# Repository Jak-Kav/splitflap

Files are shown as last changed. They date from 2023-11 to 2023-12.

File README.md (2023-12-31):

# DIY Split-Flap Display<br />(Modified by James Kavanagh (jk620))

This project is taken from `scottbez1/splitflap` and has been modofied to suit my needs.    
This is a 6 module display, with lasercut mechanical parts and base.    
I am using the chainlink system (v1.1) and the chainlink buddy (PCB version) with a lilygo T-Display.    
The system will connect to WiFi, and then NTP. It will display the time as a 24 hour clock. It will automatically adjust for daylight savings time in the UK.     
It will automaitically display 'LUNCH'  between 11:59 and 12:01 every day.     
It will automatically display 'HOME' between 16:59 and 17:01 every day.    
It will automatically display 'TINKER' between 18:00 and 18:10 on Wednesday only.    

The device will also start a bluetooth characteristic and broadcast it's current IP address. That way, you can connect to the device via bluetooth to discover it's IP address, and then connect to the webserver on the device. Oonce connected to the webserver, you are greeted with a simple HTML page where you can input a message (upto 6 characters long), and as long as it has been more than 10 minuets since the last custom message was displayed via the webserver, then your message will be displayed.    
There is also the option to manually force reset/recalibrate the device via the webserver, but you will need the password to do this (prevent spamming), and the password is in the code.

The entry point to the code is:    
`arduino/splitflap/esp32/splitflap/main.cpp`    
When editing the project, make sure you are using PlatformIO, and make sure the enviornment is set to `chainlink`. This is the only one that will work with the hardware and mechanical options implemented.

### BUILD & RELEASE
You can push commit to this repo as normal. The GitHub Actions will always bulid the firmware and confirm that it compiles and builds ok.    
If the commit is ready for a build and _RELEASE_, then simply add `*RELEASE*` to the commit message followed by `*V*` and a version number.    
I.e., `Feature X Added - *RELEASE* *V* 1.1.0` and this will build the firmware and automatically create a GitHub Release with that version number. 

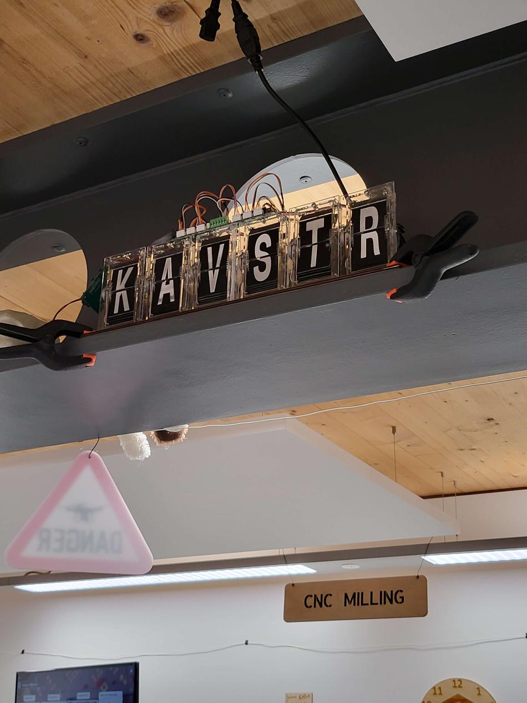
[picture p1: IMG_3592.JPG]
My Finished Display


Below is the original README:    
- - - - - -
This is a DIY [split-flap display](https://en.wikipedia.org/wiki/Split-flap_display).
Prototype four-character display: [video](https://www.youtube.com/watch?v=vq4o_88kN8g).

animated rendering
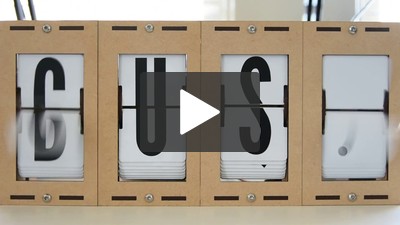
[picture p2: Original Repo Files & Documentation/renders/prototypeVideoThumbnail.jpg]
prototype video (https://www.youtube.com/watch?v=vq4o_88kN8g)






The goal is to make a low-cost display that's easy to fabricate at home in small/single quantities (e.g. custom materials can be ordered from Ponoko or similar, and other hardware is generally available).

You can view an interactive 3d model of the design on the [project website](https://scottbez1.github.io/splitflap/).

The [splitflap community Discord server](https://discord.com/invite/wgehm3PcrC) is the best place to keep up with the latest changes or ask questions about the project!

Want to help support development or just say "thanks"? Consider a one-time or monthly sponsorship:

| [:heart: Sponsor scottbez1 on GitHub](https://github.com/sponsors/scottbez1) |
|---|

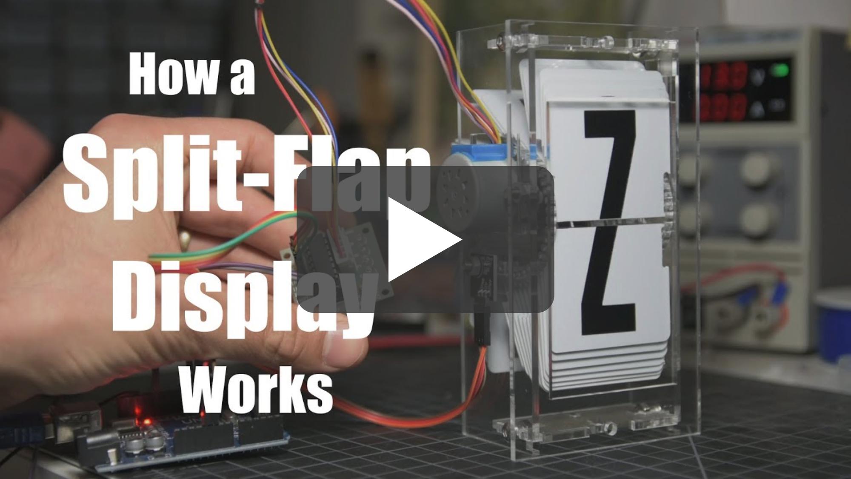
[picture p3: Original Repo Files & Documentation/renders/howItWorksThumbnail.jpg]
Video: how a split-flap display works (https://www.youtube.com/watch?v=UAQJJAQSg_g)


**Using this project in a commercial setting or for paid client work?** Go right ahead - it's open source (just make sure to follow the terms of the Apache License)! I would, however, ask that you consider [sponsoring the project](https://github.com/sponsors/scottbez1). I've been developing and maintaining this project in my free time for over 6 years, and I'd love to continue working on it. Sponsorships allow me to pay for prototypes and development tools that make this project possible. Unlike pure software projects, every iteration has real hardware costs; sponsorships allow me to keep iterating and improving the project faster. Thank you!

# Current Status
[You can download the **latest stable release** from the official 'releases' page.](https://github.com/scottbez1/splitflap/releases)

Releases have been tested and used to produce working units, but as this is a continuously evolving open-source project, there may always be minor issues and/or incomplete documentation from time to time.

| Component | Status | Notes |
| --- | --- | --- |
| Enclosure/Mechanics | *Stable* | |
| Classic Controller Electronics | *Stable* | |
| Firmware | *Stable* | |
| Control Software Example | *Stable* | Example python code for driving the display is in the [software](software) directory|

:bulb: There's a new electronics system, called the *Chainlink* system (more on this [below](#chainlink-electronics)), which makes assembly easier and supports larger displays (100+ modules), using an ESP32 for the controller. It's stable and recommended over the older "Classic" controller for new builds.

Here's a video of a large 108-module display powered by 18 Chainlink Driver boards and a Chainlink Base:

Video: animations on 108-module display (https://youtu.be/g9EPabcxBsM)

I'd love to hear your thoughts and questions about this project, and happy to incorporate any feedback you might have into these designs! Please feel free (and encouraged) to [open GitHub issues](https://github.com/scottbez1/splitflap/issues/new), email me directly, reach out [on Twitter](https://twitter.com/scottbez1), and [get involved](https://github.com/scottbez1/splitflap/pulls) in the open source development and let's keep chatting and building together!

# Build Your Own
Please note, updated documentation for the Chainlink system is still in progress; you may see outdated references to the "Classic" electronics in some documentation in the meantime. If you have any questions, please don't hesitate to ask in the [community Discord server](https://discord.gg/Hxnftc8PyW)!

* [**Ordering guide (the "easy" route) - updated for Chainlink**](https://paper.dropbox.com/doc/Splitflap-Ordering-the-easy-route--BsXzf8VyILR3nl1vUpOi28TWAg-0i6r3aqw6kZVXQOP2MyNr)
* [**Chainlink Driver Electronics User Guide**](https://paper.dropbox.com/doc/Chainlink-Driver-v1.1-Electronics-User-Guide--BsVuP9OHVo952_ZdJDBomCCzAg-U0DAXrSxEoOhgSoRU39hq)
* [**Latest stable release**](https://github.com/scottbez1/splitflap/releases)
* [**Assembly instructions (v0.5/0.6/0.7)**](https://paper.dropbox.com/doc/Splitflap-Kit-v0.5v1.0-Instructions--ASQDu1uoa6n4_t1pva1bM1MgAg-bxXJlke5ROmamcx4OH44r)

# Table of Contents
- [DIY Split-Flap Display(Modified by James Kavanagh (jk620))](#diy-split-flap-displaymodified-by-james-kavanagh-jk620)
- [Current Status](#current-status)
- [Build Your Own](#build-your-own)
- [Table of Contents](#table-of-contents)
- [Design Overview](#design-overview)
  - [Mechanical](#mechanical)
  - [Electronics](#electronics)
    - [Module Electronics](#module-electronics)
    - [Chainlink Electronics](#chainlink-electronics)
      - [Chainlink Driver](#chainlink-driver)
      - [Chainlink Buddy \[T-Display\]](#chainlink-buddy-t-display)
      - [Chainlink Buddy \[Breadboard\]](#chainlink-buddy-breadboard)
      - [Chainlink Base](#chainlink-base)
    - [Classic Controller Electronics (deprecated)](#classic-controller-electronics-deprecated)
    - [Miscellaneous Tools](#miscellaneous-tools)
      - [Flaps and Fonts](#flaps-and-fonts)
      - [3D Printed Tools](#3d-printed-tools)
      - [Chainlink Driver Tester](#chainlink-driver-tester)
  - [Code](#code)
    - [Firmware](#firmware)
    - [Computer Control Software](#computer-control-software)
- [Contributing/Modifying](#contributingmodifying)
  - [3D Design](#3d-design)
    - [Rendering](#rendering)
      - [Laser-cut vector files](#laser-cut-vector-files)
      - [Animated gif](#animated-gif)
      - [STL models/web viewer](#stl-modelsweb-viewer)
  - [Electronics Design](#electronics-design)
    - [Rendering](#rendering-1)
- [License](#license)

# Design Overview

## Mechanical
The mechanical/structural components are made from laser-cut 3mm MDF or acrylic, and held together with M4 bolts and nuts. The design is parametric and built using OpenSCAD. See below for more info on rendering/modifying the design.

2d laser cut rendering

Latest auto-generated (untested!) artifacts<sup>:warning:</sup>:
* For Ponoko 3mm MDF ([1x svg](https://s3.amazonaws.com/splitflap-artifacts/master/3d/3d_laser_vector-ponoko-3mm-mdf_1x.svg), [4x svg](https://s3.amazonaws.com/splitflap-artifacts/master/3d/3d_laser_vector-ponoko-3mm-mdf_4x.svg))
* For Ponoko 3mm acrylic ([1x svg](https://s3.amazonaws.com/splitflap-artifacts/master/3d/3d_laser_vector-ponoko-3mm-acrylic_1x.svg), [4x svg](https://s3.amazonaws.com/splitflap-artifacts/master/3d/3d_laser_vector-ponoko-3mm-acrylic_4x.svg),)
* For generic material (0.18mm kerf correction) ([1x svg](https://s3.amazonaws.com/splitflap-artifacts/master/3d/3d_laser_vector.svg))
* For Elecrow 3mm Wood ([1x zipped pdf](https://s3.amazonaws.com/splitflap-artifacts/master/3d/3d_laser_vector-elecrow-3mm-wood_1x.zip), note that Elecrow orders are automatically 5x)
* For Elecrow 3mm Acrylic ([1x zipped pdf](https://s3.amazonaws.com/splitflap-artifacts/master/3d/3d_laser_vector-elecrow-3mm-acrylic_1x.zip), note that Elecrow orders are automatically 5x)

<sup>:warning:</sup>For tested/stable/recommended artifacts, use the [latest release](https://github.com/scottbez1/splitflap/releases) instead

## Electronics
For small displays (up to 3 modules), you can skip the custom controller boards and use off-the-shelf ULN2003A driver
modules plugged into an Arduino Uno. This is [partially documented in the wiki](https://github.com/scottbez1/splitflap/wiki/Electronics#basic-prototyping-alternative-electronics-approach)
but may require some additional tinkering to get it to work. _Help wanted: if you'd like to help improve these instructions,
please reach out in the Discord server, thanks!_

The Chainlink electronics system is the current recommended design, which allows for larger-scale displays by chaining more
modules together and uses a more powerful microcontroller (ESP32) compared to the older "Classic" controller. It also adds 
the possibility of wifi and BLE control, though firmware support for this is very limited for now.

The older design ("Classic" controller board), which plugs into an Arduino Uno as a shield and can control up to 4 modules is
no longer recommended and will not receive firmware updates going forward. New builds are recommended to use the Chainlink
ESP32-based system instead.

### Module Electronics
Each module needs a hall-effect sensor for start-up calibration and fault monitoring. This can be mounted in
[different ways](https://github.com/scottbez1/splitflap/wiki/Electronics#sensor-board-alternative) but the recommended
approach is to use a small PCB, with an AH3391Q (or similar) sensor and connector, which mounts to the side of the
module with a single screw and can easily be adjusted for precise calibration.

These boards are small (about 16mm x 16 mm) and the designs are available as a panelized PCB, which can be snapped
apart. The panelization is configurable and is optimized for production at low-cost PCB fabricators like SeeedStudio, JLCPCB, or PCBWay.

<a href="https://s3.amazonaws.com/splitflap-artifacts/master/electronics/sensor-panelized-pcb-raster.png">

</a>

Latest auto-generated (untested!) artifacts<sup>:warning:</sup>:

* Sensor PCB, single ([gerbers](https://s3.amazonaws.com/splitflap-artifacts/master/electronics/sensor-jlc/gerbers.zip) / [pdf](https://s3.amazonaws.com/splitflap-artifacts/master/electronics/sensor-pcb-packet.pdf))
* Sensor PCB, panelized ([gerbers](https://s3.amazonaws.com/splitflap-artifacts/master/electronics/sensor-panelized-jlc/gerbers.zip) / [pdf](https://s3.amazonaws.com/splitflap-artifacts/master/electronics/sensor-panelized-pcb-packet.pdf))

<sup>:warning:</sup>For tested/stable/recommended artifacts, use the [latest release](https://github.com/scottbez1/splitflap/releases) instead

### Chainlink Electronics
The Chainlink system replaces the older "Classic" controller electronics and is designed to support long chains of driver boards
to control large displays (think 100+ split-flap modules). It's also designed to be easy and cheap to build, especially in higher
quantities, due to its simple BOM and surface-mount components.

The Chainlink system requires 2 core elements:
* One or more **Chainlink Driver** board. This is what interfaces with the motors and sensors of each module. Each Driver board
supports up to **6** individual split-flap modules. Chainlink Driver boards can be chained together to construct a large display.
* Some kind of ESP32 microcontroller board. There are a few options:
    * For small/medium displays, one of the **Chainlink Buddy** boards are recommended
        * **Chainlink Buddy [T-Display]**  holds a Lilygo T-Display ESP32 module which includes a built-in LCD and 2 buttons
        * **Chainlink Buddy [Breadboard]** makes it easy to connect a Chainlink Driver to a breadboard for prototyping, though you can also easily connect a Chainlink Driver to a breadboard with a few dupont wires.
    * For large displays, the **Chainlink Base** provides a number of advanced features: central
power management/distribution and fault monitoring, UART and RS-485 connections, configuration switches, and status LEDs.

#### Chainlink Driver
<a href="https://s3.amazonaws.com/splitflap-artifacts/master/electronics-chainlink/chainlinkDriver-3d.png">

</a>

Key features (compared to the older "Classic" Controller):
* Controls 6 split-flap modules per board instead of just 4 - fewer PCBs means lower cost and less wiring
* Longer PCB (200mm) gets connectors closer to each module so wires have more slack
* Primarily SMD and all components (except the pin headers and motor connectors) are available in JLCPCB's parts library
for easy SMD/THT assembly
* Clock and latch lines are buffered on each board with a 74HC125 to support longer chains
* Neopixels replaced by shift-register-driven single-color LED per module (one fewer data line needed in the chain, lower current draw, and 3.3v IO friendly)
* 2 bits of loopback (connecting 2 spare output bits on output shift registers to 2 spare inputs) allows the controller
to validate data integrity up and down the whole chain
* ~~TPL7407L mosfet low-side drivers instead of ULN2003A/MIC5842 (lower on-resistance means less voltage drop in the driver = more torque, less waste heat, and less total current consumption)~~
Due to the chip shortage, TPL7407L ICs are not currently available and will likely not be available again until mid-2022, so the auto-generated
JLC component/bom files below currently use ULN2003A darlington drivers as a suitable drop-in replacement.
* Module order goes from right-to-left since this is intended to be installed and accessed from *behind* the modules

Chainlink Driver boards are [available mostly-assembled in the Bezek Labs store](https://www.etsy.com/listing/1123280069/splitflap-chainlink-driver-v11),
and come with the additional connectors and ribbon cables you'll need. Purchases support continued development of this project.

More information on building and using Chainlink Drivers is available in the [Chainlink Driver User Guide](https://paper.dropbox.com/doc/Chainlink-Driver-v1.1-Electronics-User-Guide--BW2lxdjVkAxva68kYw2doWQEAg-U0DAXrSxEoOhgSoRU39hq).

Or if you'd like to order these directly from a fab, this design is optimized for assembly at JLCPCB, and files are automatically generated
for ordering *assembled* PCBs there. Or if you wish to assemble this board yourself instead of paying for assembly, 
you can view the [interactive BOM/placement tool](https://s3.amazonaws.com/splitflap-artifacts/master/electronics-chainlink/bom/chainlinkDriver-ibom.html)

Depending on available stock at JLCPCB, you may need to manually modify the BOM file to use alternative components, or regenerate the files
yourself using `export_jlcpcb.py` and specifying one or more `LCSC_ALT_*` field names to use a pre-selected alternative part number. See
the schematic for available pre-selected alternatives (check the symbol's properties/fields).

<a href="https://s3.amazonaws.com/splitflap-artifacts/master/electronics-chainlink/chainlinkDriver-schematic.pdf">

</a>

<a href="https://s3.amazonaws.com/splitflap-artifacts/master/electronics-chainlink/chainlinkDriver-pcb-raster.png">

</a>

Latest auto-generated (untested!) artifacts<sup>:warning:</sup>:

* Schematic [pdf](https://s3.amazonaws.com/splitflap-artifacts/master/electronics-chainlink/chainlinkDriver-schematic.pdf)
* PCB overview [pdf](https://s3.amazonaws.com/splitflap-artifacts/master/electronics-chainlink/chainlinkDriver-pcb-packet.pdf)
* PCB gerbers [zip](https://s3.amazonaws.com/splitflap-artifacts/master/electronics-chainlink/chainlinkDriver-jlc/gerbers.zip)
* PCB bom (for JLCPCB assembly) [csv](https://s3.amazonaws.com/splitflap-artifacts/master/electronics-chainlink/chainlinkDriver-jlc/bom.csv)
* PCB CPL (for JLCPCB assembly) [csv](https://s3.amazonaws.com/splitflap-artifacts/master/electronics-chainlink/chainlinkDriver-jlc/pos.csv)
* PCB bom (for manual assembly) [interactive](https://s3.amazonaws.com/splitflap-artifacts/master/electronics-chainlink/bom/chainlinkDriver-ibom.html)

<sup>:warning:</sup>For tested/stable/recommended artifacts, use the [latest release](https://github.com/scottbez1/splitflap/releases) instead

#### Chainlink Buddy \[T-Display\]
<a href="https://s3.amazonaws.com/splitflap-artifacts/master/electronics-chainlink-buddy-t-display/chainlinkBuddyTDisplay-3d.png">

</a>

The Chainlink Buddy \[T-Display\] is a convenient way to connect a T-Display ESP32 board (recommended microcontroller) to a chain
of Chainlink Drivers.

Key features:
* TTGO T-Display ESP32 module as the controller, which includes USB-C, color IPS LCD display and buttons
* Extra terminals for every pin of the T-Display allow you to connect any other peripherals to the ESP32 (the connection to the Chainlink Driver requires _only 4_ of the GPIOs)
* Optional barrel jack makes it easy to use a "wall wart" AC adapter/power-supply (since the Chainlink Driver only has screw terminals for power) -- plug in a 12V supply
and then run a wire from the onboard screw terminals to the Chainlink Driver's motor power screw terminals.
* Optional 5V regulator allows for powering the ESP32 without a USB connection, using the 12V motor power supply

Chainlink Buddy \[T-Display\] boards are [available in the Bezek Labs store](https://www.etsy.com/listing/1109357786/splitflap-chainlink-buddy-t-display),
and come with the additional connectors you'll need. Purchases support continued development of this project. 

<a href="https://s3.amazonaws.com/splitflap-artifacts/master/electronics-chainlink-buddy-t-display/chainlinkBuddyTDisplay-schematic.pdf">

</a>

<a href="https://s3.amazonaws.com/splitflap-artifacts/master/electronics-chainlink-buddy-t-display/chainlinkBuddyTDisplay-pcb-raster.png">

</a>

Latest auto-generated (untested!) artifacts<sup>:warning:</sup>:

* Schematic [pdf](https://s3.amazonaws.com/splitflap-artifacts/master/electronics-chainlink-buddy-t-display/chainlinkBuddyTDisplay-schematic.pdf)
* PCB ([gerbers](https://s3.amazonaws.com/splitflap-artifacts/master/electronics-chainlink-buddy-t-display/chainlinkBuddyTDisplay-jlc/gerbers.zip) / [pdf](https://s3.amazonaws.com/splitflap-artifacts/master/electronics-chainlink-buddy-t-display/chainlinkBuddyTDisplay-pcb-packet.pdf))
* Panelized PCB ([gerbers](https://s3.amazonaws.com/splitflap-artifacts/master/electronics-chainlink-buddy-t-display/chainlinkBuddyTDisplay-panelized-jlc/gerbers.zip) / [pdf](https://s3.amazonaws.com/splitflap-artifacts/master/electronics-chainlink-buddy-t-display/chainlinkBuddyTDisplay-panelized-pcb-packet.pdf))
* PCB bom (for manual assembly) [interactive](https://s3.amazonaws.com/splitflap-artifacts/master/electronics-chainlink-buddy-t-display/bom/chainlinkBuddyTDisplay-ibom.html)

<sup>:warning:</sup>For tested/stable/recommended artifacts, use the [latest release](https://github.com/scottbez1/splitflap/releases) instead

#### Chainlink Buddy \[Breadboard\]
<a href="https://s3.amazonaws.com/splitflap-artifacts/master/electronics-chainlink-buddy-breadboard/chainlinkBuddyBreadboard-3d.png">

</a>

The Chainlink Buddy \[Breadboard\] makes it easy to connect a Chainlink Driver to a breadboard for prototyping. You could use 5 dupont wires and have a
messy rats nest, or you could use a single ribbon cable and this slick breakout board.

Chainlink Buddy \[Breadboard\] boards are [available in the Bezek Labs store](https://www.etsy.com/listing/1123863267/splitflap-chainlink-buddy-breadboard),
and come with the additional connectors you'll need. Purchases support continued development of this project. 

<a href="https://s3.amazonaws.com/splitflap-artifacts/master/electronics-chainlink-buddy-breadboard/chainlinkBuddyBreadboard-schematic.pdf">

</a>

<a href="https://s3.amazonaws.com/splitflap-artifacts/master/electronics-chainlink-buddy-breadboard/chainlinkBuddyBreadboard-pcb-raster.png">

</a>

Latest auto-generated (untested!) artifacts<sup>:warning:</sup>:

* Schematic [pdf](https://s3.amazonaws.com/splitflap-artifacts/master/electronics-chainlink-buddy-breadboard/chainlinkBuddyBreadboard-schematic.pdf)
* PCB ([gerbers](https://s3.amazonaws.com/splitflap-artifacts/master/electronics-chainlink-buddy-breadboard/chainlinkBuddyBreadboard-jlc/gerbers.zip) / [pdf](https://s3.amazonaws.com/splitflap-artifacts/master/electronics-chainlink-buddy-breadboard/chainlinkBuddyBreadboard-pcb-packet.pdf))
* Panelized PCB ([gerbers](https://s3.amazonaws.com/splitflap-artifacts/master/electronics-chainlink-buddy-breadboard/chainlinkBuddyBreadboard-panelized-jlc/gerbers.zip) / [pdf](https://s3.amazonaws.com/splitflap-artifacts/master/electronics-chainlink-buddy-breadboard/chainlinkBuddyBreadboard-panelized-pcb-packet.pdf))
* PCB bom (for manual assembly) [interactive](https://s3.amazonaws.com/splitflap-artifacts/master/electronics-chainlink-buddy-breadboard/bom/chainlinkBuddyBreadboard-ibom.html)

<sup>:warning:</sup>For tested/stable/recommended artifacts, use the [latest release](https://github.com/scottbez1/splitflap/releases) instead

#### Chainlink Base
<a href="https://s3.amazonaws.com/splitflap-artifacts/master/electronics-chainlink-base/chainlinkBase-3d.png">

</a>

This has been tested and appears to work, but is not yet recommended for general use. Firmware support is in progress.

The Chainlink Base PCB is an optional alternative to a Chainink Buddym, designed for particularly large displays.
It hosts the ESP32 and adds additional connectivity options (terminals for UART and RS485 serial) and
power distribution (independently-monitored power channels for multiple "zones" of Driver boards).

Key features:
* TTGO T-Display ESP32 module as the controller, which includes USB-C, color IPS LCD display and buttons
* Optional master relay output for 12V PSU control (5V relay, up to ~500mA coil current)
  * Future firmware will power on the 12V PSU after a startup self-test, and power off PSU in case of any faults
* 5 channels of independently monitored 12V switches for powering groups of Chainlink Driver boards (6-10A max per channel)
  * Depending on the motors you use, each channel may be able to power about 6 Chainlink Driver boards which is 36 splitflap modules
  * Each channel includes an automotive fuse holder for additional over-current protection
  * INA219 and shunt resistor provide high fidelity voltage and current monitoring 
  * Firmware will power on each channel after a startup self-test, and power off the channel in case of any faults
  * 3.3V output for powering many Chainlink Driver boards
* Flexible controller input power
  * USB power from the T-Display works by default, though external power is recommended for larger displays
  * Regulated 5V can be connected directly to the screw terminals, or
  * if you are using an always-on 12V PSU without a master relay, you can install a buck module and power the board from 12V using the 7-28V screw terminals

<a href="https://s3.amazonaws.com/splitflap-artifacts/master/electronics-chainlink-base/chainlinkBase-schematic.pdf">

</a>

<a href="https://s3.amazonaws.com/splitflap-artifacts/master/electronics-chainlink-base/chainlinkBase-pcb-raster.png">

</a>

Latest auto-generated (untested!) artifacts<sup>:warning:</sup>:

* Schematic [pdf](https://s3.amazonaws.com/splitflap-artifacts/master/electronics-chainlink-base/chainlinkBase-schematic.pdf)
* PCB overview [pdf](https://s3.amazonaws.com/splitflap-artifacts/master/electronics-chainlink-base/chainlinkBase-pcb-packet.pdf)
* PCB gerbers [zip](https://s3.amazonaws.com/splitflap-artifacts/master/electronics-chainlink-base/chainlinkBase-jlc/gerbers.zip)
* PCB bom (for manual assembly) [interactive](https://s3.amazonaws.com/splitflap-artifacts/master/electronics-chainlink-base/bom/chainlinkBase-ibom.html)

<sup>:warning:</sup>There are currently no stable releases of this board. Once the board design is tested and recommended, a stable release will be created on the [Releases dashboard](https://github.com/scottbez1/splitflap/releases)

### Classic Controller Electronics (deprecated)
The Classic driver board is not recommended for new designs.

The Classic controller board is designed to plug into an Arduino like a shield, and can control 4 stepper motors.
Up to 3 driver boards can be chained together, for up to 12 modules controlled by a single Arduino.
The designs for the controller can be found under [`electronics/splitflap.pro`](electronics/splitflap.pro) (KiCad 5 project).
Nearly everything is a through-hole component rather than SMD, so it's very easy to hand-solder.

The driver uses 2 MIC5842 low-side shift-register drivers, with built-in transient-suppression diodes, to control the motors, and a 74HC165 shift register to read from 4 hall-effect magnetic home position sensors.
There are optional WS2812B RGB LEDs which can be used to indicate the status of each of the 4 channels.

<a href="https://s3.amazonaws.com/splitflap-artifacts/master/electronics-classic/classic-schematic.pdf">

</a>

The PCB layout is 10cm x 5cm which makes it fairly cheap to produce using a low-cost PCB manufacturer (e.g. Seeed Studio).

<a href="https://s3.amazonaws.com/splitflap-artifacts/master/electronics-classic/classic-pcb-raster.png">

</a>

Latest auto-generated (untested!) artifacts<sup>:warning:</sup>:

* Bill of Materials ([csv](https://s3.amazonaws.com/splitflap-artifacts/master/electronics-classic/bom/splitflap-bom.csv), [interactive](https://s3.amazonaws.com/splitflap-artifacts/master/electronics-classic/bom/splitflap-ibom.html))
* PCB ([gerbers](https://s3.amazonaws.com/splitflap-artifacts/master/electronics-classic/classic-jlc/gerbers.zip) / [pdf](https://s3.amazonaws.com/splitflap-artifacts/master/electronics-classic/classic-pcb-packet.pdf))
* Panelized PCB ([gerbers](https://s3.amazonaws.com/splitflap-artifacts/master/electronics-classic/classic-panelized-jlc/gerbers.zip) / [pdf](https://s3.amazonaws.com/splitflap-artifacts/master/electronics-classic/classic-panelized-pcb-packet.pdf))

<sup>:warning:</sup>For tested/stable/recommended artifacts, use the [latest release](https://github.com/scottbez1/splitflap/releases) instead

### Miscellaneous Tools

#### Flaps and Fonts
If you'd like to print your own flaps, or cut custom vinyl letter stickers, the project includes a script to generate vector design files
that is extremely configurable:

* Font for text (this is further customizable in OpenSCAD)
* Character-set - which letters/numbers/symbols/colors are included and in what order
* Bleed - extends rendering past the borders of the flaps to compensate for slight misalignment of printing and cutting operations
* Keepout areas - option to highlight keepout violations for manual review, automatically clip them, or ignore them
* Rendering options:
    * Single-sided - useful for previewing how all letters will look on flaps
    * Front/back - for batch duplex printing, generate separate front-side and back-side files (e.g. sign shop printing on a flat sheet of PVC)
    * Side-by-side - for individual flap printing, each flap's front design is laid out side-by-side with its back design

TODO: finish documenting this and render some example images...

#### 3D Printed Tools
The project also includes a number of optional 3D printed designs to make assembly easier. These include:

* [a flap scoring jig](3d/tools/scoring_jig.scad) for precisely marking the cut point when splitting CR80 cards
* [a flap punch jig](3d/tools/punch_jig.scad) for aligning the punch when making the pin cutouts on either side of a flap
* [a flap container](3d/tools/flap_container.scad) for storing and organizing stacks of completed flaps
* [a sensor PCB holder](3d/tools/pcb_case.scad) for storing and protecting soldered sensor boards

All of these designs are parametric and customizable within OpenSCAD. To print them, open up the relevant file in OpenSCAD and use `File -> Export -> Export as STL` to render the design as an STL file for your slicer.

#### Chainlink Driver Tester
<a href="https://s3.amazonaws.com/splitflap-artifacts/master/electronics-chainlink-tester/chainlinkDriverTester-3d.png">

</a>

This is not likely to be useful unless you're planning to manufacture dozens to hundreds of Chainlink Driver boards, but the Chainlink Driver Tester is a complete testbed
for Chainlink Driver boards as they come assembled by the PCBA fabricator.

This is currently under very active development.

Key features:
* TTGO T-Display (ESP32) controller, screen, and buttons for controlling tests and reporting results
* Pogo-pins for all connectors on the Chainlink Driver board-under-test (screw terminals, sensor pin headers, and motor connectors)
* 12V switch to supply motor power to the board-under-test, with automotive fuse and INA219 voltage/current monitoring (based on the Chainlink Base channel switch design)
* Separate 3.3V supply for the board-under-test, protected with a polyfuse, should avoid browning out the Tester's MCU in case of 3.3V short-circuits
* Motor and sensor connections are broken out from the pogo-pins for a full closed-loop hardware test
* Screw terminals to chain another Chainlink Driver (not under test) to validate that chained outputs work on the board-under-test
* MCP23017 GPIO expander with 8 GPIO pins exposed via headers for future expansion inputs
* Large cutout allows a barcode scanner or camera to be aimed at the bottom of the board-under-test for tracking serial numbers.
* Buzzer option for audible pass/fail feedback

<a href="https://s3.amazonaws.com/splitflap-artifacts/master/electronics-chainlink-tester/chainlinkDriverTester-schematic.pdf">

</a>

<a href="https://s3.amazonaws.com/splitflap-artifacts/master/electronics-chainlink-tester/chainlinkDriverTester-pcb-raster.png">

</a>

Latest auto-generated (untested!) artifacts<sup>:warning:</sup>:

* Schematic [pdf](https://s3.amazonaws.com/splitflap-artifacts/master/electronics-chainlink-tester/chainlinkDriverTester-schematic.pdf)
* PCB overview [pdf](https://s3.amazonaws.com/splitflap-artifacts/master/electronics-chainlink-tester/chainlinkDriverTester-pcb-packet.pdf)
* PCB gerbers [zip](https://s3.amazonaws.com/splitflap-artifacts/master/electronics-chainlink-tester/chainlinkDriverTester-jlc/gerbers.zip)
* PCB bom (for manual assembly) [interactive](https://s3.amazonaws.com/splitflap-artifacts/master/electronics-chainlink-tester/bom/chainlinkDriverTester-ibom.html)

<sup>:warning:</sup>There are currently no stable releases of this board, and there may never be as it is a niche production tool, not an end product. If you
need this tool, you are likely actively involved in development and should understand the revision history and current status of development enough to make
an informed decision about which revision(s) to use.

## Code
### Firmware
The driver firmware is written using Arduino and is available at [`arduino/splitflap/Splitflap/Splitflap.ino`](arduino/splitflap/Splitflap/Splitflap.ino). 

The firmware implements a closed-loop controller that accepts letters as input over USB serial and drives the stepper motors using a precomputed acceleration ramp for smooth control. The firmware automatically calibrates the spool position at startup, using the hall-effect magnetic sensor, and will automatically recalibrate itself if it ever detects that the spool position has gotten out of sync. If a commanded rotation is expected to bring the spool past the "home" position, it will confirm that the sensor is triggered neither too early nor too late; otherwise it will search for the "home" position to get in sync before continuing to the desired letter.

### Computer Control Software
The display can be controlled by a computer connected to the Arduino over USB serial. A basic python library for interfacing with the Arduino and a demo application that displays random words can be found in the [software](software) directory.

Commands to the display are sent in a basic plain-text format, and messages _from_ the display are single-line JSON objects, always with a `type` entry describing which type of message it is.

When the Arduino starts up, it sends an initialization message that looks like:
```
{"type":"init", "num_modules":4}
```

The display will automatically calibrate all modules, and when complete it will send a status update message:
```
{
    "type":"status",
    "modules":[
        {"state":"normal", "flap":" ", "count_missed_home":0, "count_unexpected_home":0},
        {"state":"sensor_error", "flap":"e", "count_missed_home":0, "count_unexpected_home":0},
        {"state":"sensor_error", "flap":"e", "count_missed_home":0, "count_unexpected_home":0},
        {"state":"sensor_error", "flap":"e", "count_missed_home":0, "count_unexpected_home":0}
    ]
}
```
(Note: this is sent as a single line, but has been reformatted for readability above)

In this case the Arduino was programmed to support 4 modules, but only 1 module is connected, so the other 3 end up in `"sensor_error"` state. More on status updates below.

At this point you can command the display to show some letters. To do this, send a message to the Arduino that looks like this:
```
=hiya\n
```
The `=` indicates a movement command, followed by any number of letters, followed by a newline. You don't have to send the exact number of modules - if you send fewer letters than modules, only the first N modules will be updated and the remainder won't move. For instance, you could send `=a\n` as shorthand to only set the first module (even if there are 12 modules connected). Any letters that can't be displayed are considered a no-op for that module.

Whenever ALL modules come to a stop, the Arduino will send a status update message (just like the one following initialization, shown above). Here's what the fields mean in each module's status entry:
- **state** - `normal` indicates it's working as intended, `sensor_error` indicates the module can't find the home position and has given up trying (it will no longer respond to movement commands until told to recalibrate - see below). `panic` indicates the firmware detected a programming bug and has gone into failsafe mode (it will no longer respond to movement commands and requires a full reset of the Arduino to recover - should never happen).
- **flap** - which letter is shown by this module
- **count\_missed\_home** - number of times the module expected to pass the home position but failed to detect it. If this is non-zero, it indicates either a flaky sensor or that the motor may have jammed up. The module automatically attempts to recalibrate whenever it misses the home position, so if this number is non-zero and the module is still in the `normal` state, it means the module successfully recovered from the issue(s). However, if this number keeps going up over continued use, it may indicate a recurrent transient issue that warrants investigation.
- **count\_unexpected\_home** - number of times the module detected the home position when it wasn't supposed to. This is rare, but would indicate a flaky/broken sensor that is tripping at the wrong time. Just like with missed home errors, unexpected home errors will cause the module to attempt to recalibrate itself.

If you want to make all modules recalibrate their home position, send a single @ symbol (no newline follows):
```
@
```
This recalibrates all modules, including any that were in the `sensor_error` state; if recalibration succeeds they will return to the `normal` state and start responding to movement commands again.

# Contributing/Modifying

Looking to make some modifications or play around with the design on your local machine? Jump right in! Note that all of the scripts and automation are developed for Ubuntu. Mac OS support is planned,
but not currently implemented (but feel free to open a PR if you want to help!).

## 3D Design

The main design file is [`3d/splitflap.scad`](3d/splitflap.scad)

You'll need a recent version of OpenSCAD (e.g. 2015-03), which may need to be installed through the PPA:
`sudo add-apt-repository ppa:openscad/releases`

In general, solid objects such as the enclosure sides or spool components are built from 2d primitives and then extruded to the appropriate thickness for 3d rendering, rather than using 3d primitives. This simplifies the design without losing expressiveness; the perpendicular laser cut beam doesn't allow for cuts that vary in the Z dimension anyway.

Note that while the design is parameterized and many values may be tweaked, there is currently no error checking for invalid parameters or combinations of parameters. Please take care to validate the design if you change any parameters. For instance, while most of the design will adjust to a changed `num_modules` value, certain values may cause some elements to intersect with other elements or protrude beyond their expected dimensions.

### Rendering
#### Laser-cut vector files
The design can be rendered to 2d for laser cutting by running [`3d/scripts/generate_2d.py [--panelize <number>]`](3d/scripts/generate_2d.py), which outputs to `3d/build/laser_parts/combined.svg`. The optional `--panelize` argument allows for rendering a panel of modules in a single SVG, for bulk laser-cutting.

Internally, the design uses a `projection_renderer` module ([`3d/projection_renderer.scad`](3d/projection_renderer.scad)), which takes a list of child elements to render, and depending on the `render_index` renders a single child at a time. It also _adds_ material to each shape to account for the kerf that will be cut away by the laser.

The [`generate_2d.py`](3d/scripts/generate_2d.py) script interacts with the `projection_renderer` module by first using it to determine the number of subcomponents to render, then runs OpenSCAD to export each component to an SVG file. It does some post-processing on the SVG output (notably adds "mm" to the document dimensions), and then combines all components into the single `combined.svg` output.

Once the `combined.svg` file is generated, you'll want to double-check there aren't any redundant cut lines that are shared by multiple adjacent pieces, to save time/cost when cutting. They should be detected automatically (and highlighted in red in the rendering above), but it doesn't hurt to double-check. In Inkscape, select the "Edit paths by nodes" tool and select an edge to delete - the endpoints should turn blue. Then click "Delete segment between two non-endpoint nodes", and repeat this for all other redundant cut lines.

#### Animated gif
The design can be rendered to a rotating 3d animated gif (seen above) by running [`3d/scripts/generate_gif.py`](3d/scripts/generate_gif.py), which outputs to `3d/build/animation/animation.gif`

The `generate_gif.py` script runs multiple OpenSCAD instances in parallel to render the design from 360 degrees to individual png frames, which are then combined into the final gif animation. As part of building the animation, `generate_gif.py` renders the design with multiple configurations (opaque enclosure, see-through enclosure, no-enclosure and no flaps) by setting the `render_enclosure` and `render_flaps` variables.

#### STL models/web viewer
The design can be rendered to a series of STL files (one per color used in the model) in order to be displayed in an [interactive web-based 3d viewer](https://scottbez1.github.io/splitflap/). Similar to the `projection_renderer` used to render individual components for laser-cutting, the [ColoredStlExporter](3d/scripts/colored_stl_exporter.py) detects all the colors used in the model and renders them one-by-one to separate STL files, along with a manifest that maps each STL file to its RGB color. The STL files and manifest are loaded using three.js to display an interactive model on a web site using WebGL. See this blog post for more details on how the export and three.js renderer work: [OpenSCAD Rendering Tricks, Part 3: Web viewer](http://scottbezek.blogspot.com/2016/08/openscad-rendering-tricks-part-3-web.html).

## Electronics Design
All of the electronics are developed using KiCad 5. Panelization is provided by [KiKit](https://github.com/yaqwsx/KiKit) and gerber/BOM generation is provided by [KiBot](https://github.com/INTI-CMNB/KiBot).

### Rendering
The mechanical and electrical design renderings and links above are automatically updated on every commit with the latest rendering. See this blog post for more details on how that works: [Automated KiCad, OpenSCAD rendering using Travis CI](http://scottbezek.blogspot.com/2016/04/automated-kicad-openscad-rendering.html).

The PCB layout can be rendered to an svg or png (seen above) by running [`electronics/scripts/generate_svg.py file.kicad_pcb`](electronics/scripts/generate_svg.py).
This uses KiCad's [Python scripting API](https://docs.kicad-pcb.org/doxygen/md_Documentation_development_pcbnew-plugins.html)
to render several layers to individual svg files, manipulates them to apply color and opacity settings, and then merges them to a single svg.
For additional details, see this blog post: [Scripting KiCad Pcbnew exports](http://scottbezek.blogspot.com/2016/04/scripting-kicad-pcbnew-exports.html).

For reviewing the design, a pdf packet with copper, silkscreen, and drill info can be produced by running [`electronics/scripts/generate_pdf.py file.kicad_pcb`](electronics/scripts/generate_pdf.py).

Gerber files for fabrication can be exported by running [`electronics/scripts/generate_gerber.py file.kicad_pcb`](electronics/scripts/generate_gerber.py).
This generates gerber files and an Excellon drill file with Seeed Studio's [naming conventions](http://support.seeedstudio.com/knowledgebase/articles/1176532-how-to-generate-the-gerber-manufacturing-files) and produces a `.zip` which can be sent for fabrication.

EESchema isn't easily scriptable, so to export the schematic [`electronics/scripts/export_schematic.py`](electronics/scripts/export_schematic.py) starts an X Virtual Frame Buffer (Xvfb) and open the `eeschema` GUI within that virtual display, and then send a series of hardcoded key presses via `xdotool` to interact with the GUI and click through the dialogs. This is very fragile but seems to work ok for now. For additional details, see this blog post: [Using UI automation to export KiCad schematics](http://scottbezek.blogspot.com/2016/04/automated-kicad-schematic-export.html).

# License
I'd love to hear your thoughts and questions about this project, and happy to incorporate any feedback you might have into these designs! Please feel free (and encouraged) to [open GitHub issues](https://github.com/scottbez1/splitflap/issues/new), email me directly, reach out [on Twitter](https://twitter.com/scottbez1), and [get involved](https://github.com/scottbez1/splitflap/pulls) in the open source development and let's keep chatting and building together!

This project is licensed under Apache v2 (see [LICENSE.txt](LICENSE.txt)).

    Copyright 2015-2021 Scott Bezek and the splitflap contributors
    
    Licensed under the Apache License, Version 2.0 (the "License");
    you may not use this file except in compliance with the License.
    You may obtain a copy of the License at
    
        http://www.apache.org/licenses/LICENSE-2.0
    
    Unless required by applicable law or agreed to in writing, software
    distributed under the License is distributed on an "AS IS" BASIS,
    WITHOUT WARRANTIES OR CONDITIONS OF ANY KIND, either express or implied.
    See the License for the specific language governing permissions and
    limitations under the License.

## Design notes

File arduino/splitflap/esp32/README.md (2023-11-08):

This folder contains extra source files to replace the main (Splitflap.ino)
source file when building for ESP32 via PlatformIO. See the "esp32"
enviornment definition in platformio.ini for more info about how these files
are included.

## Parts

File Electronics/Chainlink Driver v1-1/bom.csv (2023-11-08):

Comment | Designator | Footprint | LCSC
74HC595 | U1,U5,U7,U9 | ModifiedSymbols:SOIC-16_3.9x9.9mm_P1.27mm_silk | C5947
MountingHole | H1,H2,H3,H4,H5 | MountingHole:MountingHole_3.2mm_M3_ISO7380_Pad
0.1uF | C2,C4,C5,C7,C6,C1,C9,C10,C12,C11 | Capacitor_SMD:C_0603_1608Metric | C14663
TPL7407L | U2,U6,U10,U8 | ModifiedSymbols:SOIC-16_3.9x9.9mm_P1.27mm_silk | C7512
Motor A | J3 | Connector_JST:JST_XH_B5B-XH-A_1x05_P2.50mm_Vertical
Motor B | J5 | Connector_JST:JST_XH_B5B-XH-A_1x05_P2.50mm_Vertical
Motor C | J6 | Connector_JST:JST_XH_B5B-XH-A_1x05_P2.50mm_Vertical
Motor D | J7 | Connector_JST:JST_XH_B5B-XH-A_1x05_P2.50mm_Vertical
74HC165 | U4 | ModifiedSymbols:SOIC-16_3.9x9.9mm_P1.27mm_silk | C5613
100uF | C3 | Capacitor_SMD:CP_Elec_8x10 | C176665
10uF | C8 | Capacitor_SMD:CP_Elec_4x5.3 | C134721
LED A | D1 | ModifiedSymbols:LED_0603_1608Metric_Silkscreen | C2286
LED B | D2 | ModifiedSymbols:LED_0603_1608Metric_Silkscreen | C2286
LED C | D3 | ModifiedSymbols:LED_0603_1608Metric_Silkscreen | C2286
LED D | D4 | ModifiedSymbols:LED_0603_1608Metric_Silkscreen | C2286
220R | R2,R3,R4,R5,R1,R10 | Resistor_SMD:R_0603_1608Metric | C22962
Sensor A | J8 | Connector_PinHeader_2.54mm:PinHeader_1x03_P2.54mm_Vertical
Sensor B | J9 | Connector_PinHeader_2.54mm:PinHeader_1x03_P2.54mm_Vertical
Sensor C | J10 | Connector_PinHeader_2.54mm:PinHeader_1x03_P2.54mm_Vertical
Sensor D | J11 | Connector_PinHeader_2.54mm:PinHeader_1x03_P2.54mm_Vertical
47k | R6,R7,R8,R9,R11,R12,R14 | Resistor_SMD:R_0603_1608Metric | C25819
Motor E | J12 | Connector_JST:JST_XH_B5B-XH-A_1x05_P2.50mm_Vertical
Motor F | J13 | Connector_JST:JST_XH_B5B-XH-A_1x05_P2.50mm_Vertical
LED E | D5 | ModifiedSymbols:LED_0603_1608Metric_Silkscreen | C2286
LED F | D6 | ModifiedSymbols:LED_0603_1608Metric_Silkscreen | C2286
Sensor E | J14 | Connector_PinHeader_2.54mm:PinHeader_1x03_P2.54mm_Vertical
Sensor F | J15 | Connector_PinHeader_2.54mm:PinHeader_1x03_P2.54mm_Vertical
74HC125 | U3 | ModifiedSymbols:SOIC-14_3.9x8.7mm_P1.27mm_silk | C5598
MountingHole | H6,H7 | JLCPCB:AssemblyToolingHole
Power | J16,J17,J18 | ScrewTerminals:Generic-5.08-2P | C395868
Input | J19 | ModifiedSymbols:IDC-Header_2x04_P2.54mm_Vertical
Output | J20 | ModifiedSymbols:IDC-Header_2x04_P2.54mm_Vertical

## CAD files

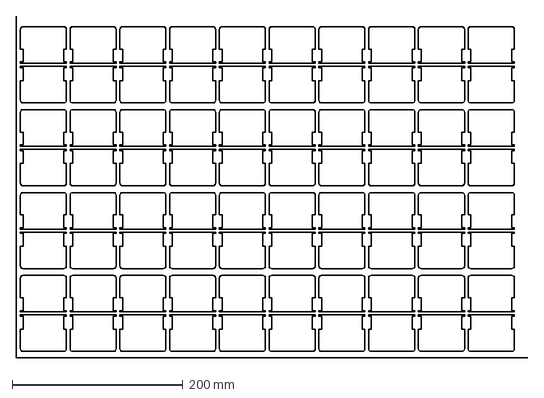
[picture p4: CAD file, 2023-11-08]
Custom Flaps/10 by 8 Flaps.dxf
600.0 x 400.0 mm

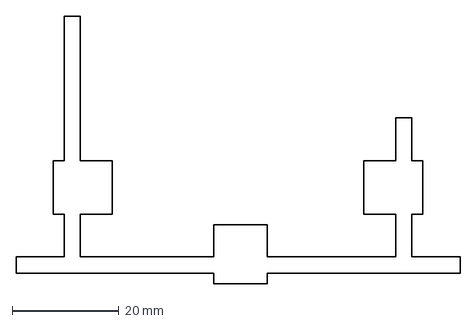
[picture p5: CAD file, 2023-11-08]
Footprint for base stand.dxf
83.0 x 50.0 mm

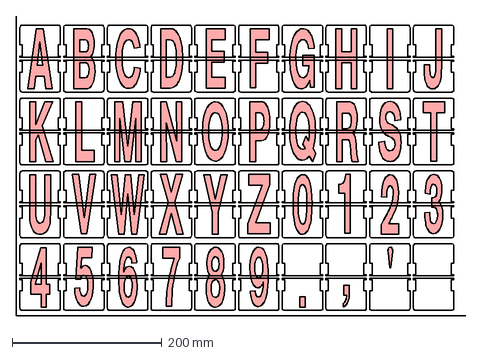
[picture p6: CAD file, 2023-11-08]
Custom Flaps/10 by 8 Flaps with chars.dxf
600.0 x 400.0 mm

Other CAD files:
Original Repo Files & Documentation/3d/global_constants.scad
Original Repo Files & Documentation/3d/sensor_pcb_dimensions.scad
Original Repo Files & Documentation/3d/28byj-48.scad
Original Repo Files & Documentation/3d/assert.scad
Original Repo Files & Documentation/3d/color_util.scad
Original Repo Files & Documentation/3d/combined_front_panel.scad
Original Repo Files & Documentation/3d/flap.scad
Original Repo Files & Documentation/3d/flap_dimensions.scad
Original Repo Files & Documentation/3d/flap_fonts.scad
Original Repo Files & Documentation/3d/font_generator.scad
Original Repo Files & Documentation/3d/label.scad
Original Repo Files & Documentation/3d/m4_dimensions.scad
Original Repo Files & Documentation/3d/pcb.scad
Original Repo Files & Documentation/3d/projection_renderer.scad
Original Repo Files & Documentation/3d/rough7380.scad
Original Repo Files & Documentation/3d/shapes.scad
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

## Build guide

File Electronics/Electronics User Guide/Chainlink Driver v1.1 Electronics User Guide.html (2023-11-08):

(https://paper.dropbox.com/)

Splitflap Public Documentation (https://paper.dropbox.com/folder/show/Splitflap-Public-Documentation-e.1gg8YzoPEhbTkrhvQwJ2zzxMuSCUJPNPzKFBvsogXuWLTH6vNRoM)

Visible to members of this folder

Chainlink Driver v1.1 Electronics User Guide (https://paper.dropbox.com/doc/Chainlink-Driver-v1.1-Electronics-User-Guide-U0DAXrSxEoOhgSoRU39hq)

 (https://paper.dropbox.com/)

Sign inSign up

Chainlink Driver v1.1 Electronics User Guide

<< Back to Documentation Index (https://paper.dropbox.com/doc/Splitflap-Documentation-Index--BfK6yrHXvLHu_lqLxHSyabHuAg-9t3gJyFBoD3vKI3Tl5VDb)

# Intro

If you’re just getting started and want to learn more about the Chainlink Driver, jump to the bottom of this document (https://paper.dropbox.com/doc/Chainlink-Driver-v1.1-User-Guide-BWhbqC5xa02TlskitjhIE95eAg-U0DAXrSxEoOhgSoRU39hq) which includes some more background and general info.

Please let me know if you have any questions or suggestions on how to improve these instructions - either leave a comment inline below (need to be logged into Dropbox to do so, I believe) or else email me directly at scottbez1 at gmail.com.

Building a split-flap display? I would love to hear from you and see photos/videos of your project in progress or completed! This project has been a hobby of mine for a few years and the coolest part by far is hearing from other people making their own and seeing them in action. Feel free to shoot me an email at scottbez1 at gmail.com 🙂 or, join the Discord server (https://discord.gg/wgehm3PcrC), to share and discuss with the wider split-flap community!

# 1. Gather the parts

- Chainlink Driver PCB assembly (see appendix (https://paper.dropbox.com/doc/Chainlink-Driver-v1.1-User-Guide--BWhbqC5xa02TlskitjhIE95eAg-U0DAXrSxEoOhgSoRU39hq) for ordering info)
- Connectors (all included with the Chainlink Driver boards I sell on Etsy)
- 6x JST XH 5-pin
- 6x 3-pin male headers
- 2x 8-pin 2-row shrouded IDC connectors
- Wires
- 8-pin 1.27mm ribbon cable, and IDC connectors for each end (included with the Chainlink Driver boards I sell on Etsy)
- 3.3v power wire
- e.g. 22AWG solid hookup wire
- 12v power/ground wires
- 20AWG up to 14AWG depending on number of modules
- 12V Power supply (see appendix (https://paper.dropbox.com/doc/Chainlink-Driver-v1.1-User-Guide--BWhbqC5xa02TlskitjhIE95eAg-U0DAXrSxEoOhgSoRU39hq) for more info)
- ESP32

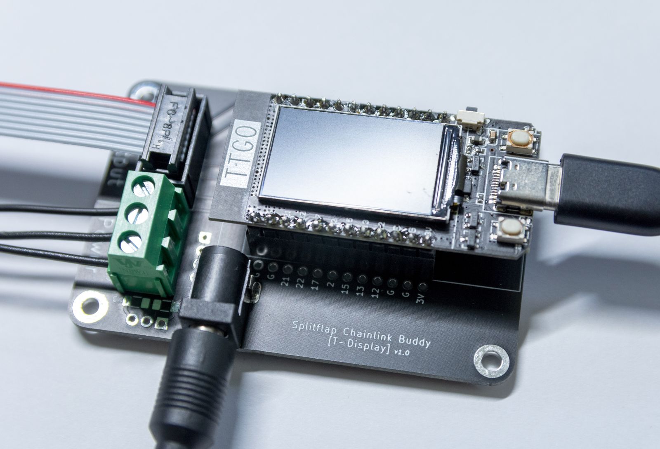
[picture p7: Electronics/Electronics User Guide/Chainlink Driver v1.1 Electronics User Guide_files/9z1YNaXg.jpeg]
User-uploaded image: DSC_5014_s.jpg


Chainlink Buddy [T-Display]

- The TTGO T-Display (https://amzn.to/3kHwhMm) [affiliate links help support this project at no cost to you, or use a non-affiliate link (https://www.amazon.com/LILYGO-T-Display-Arduino-Development-CH9102F/dp/B099MPFJ9M) if you’d prefer] is the recommended ESP32 board, which includes a 240x135 LCD that the splitflap firmware supports out of the box. (Also available on aliexpress (https://www.aliexpress.com/item/33048962331.html), which may be cheaper)
- An optional Chainlink Buddy (https://www.etsy.com/listing/1109357786/splitflap-chainlink-buddy-t-display) (https://www.etsy.com/listing/1109357786/splitflap-chainlink-buddy-t-display)[T-Display] (https://www.etsy.com/listing/1109357786/splitflap-chainlink-buddy-t-display) is also highly recommended for most users, which makes it easy and clean to connect a T-Display to the Chainlink Driver.
- If you want to use an ESP32 module other than a T-Display, a Chainlink Buddy (https://www.etsy.com/listing/1123863267/splitflap-chainlink-buddy-breadboard) (https://www.etsy.com/listing/1123863267/splitflap-chainlink-buddy-breadboard)[Breadboard] (https://www.etsy.com/listing/1123863267/splitflap-chainlink-buddy-breadboard) may be helpful in lieu of the T-Display Buddy. See the appendix (https://paper.dropbox.com/doc/Chainlink-Driver-v1.1-User-Guide-BWhbqC5xa02TlskitjhIE95eAg-U0DAXrSxEoOhgSoRU39hq) for more info on using other ESP32 modules.

# 2. Finish assembling the PCB

- Insert and solder the connectors as shown. Note that both of the IDC connectors on the ends face the same way - notches facing left.

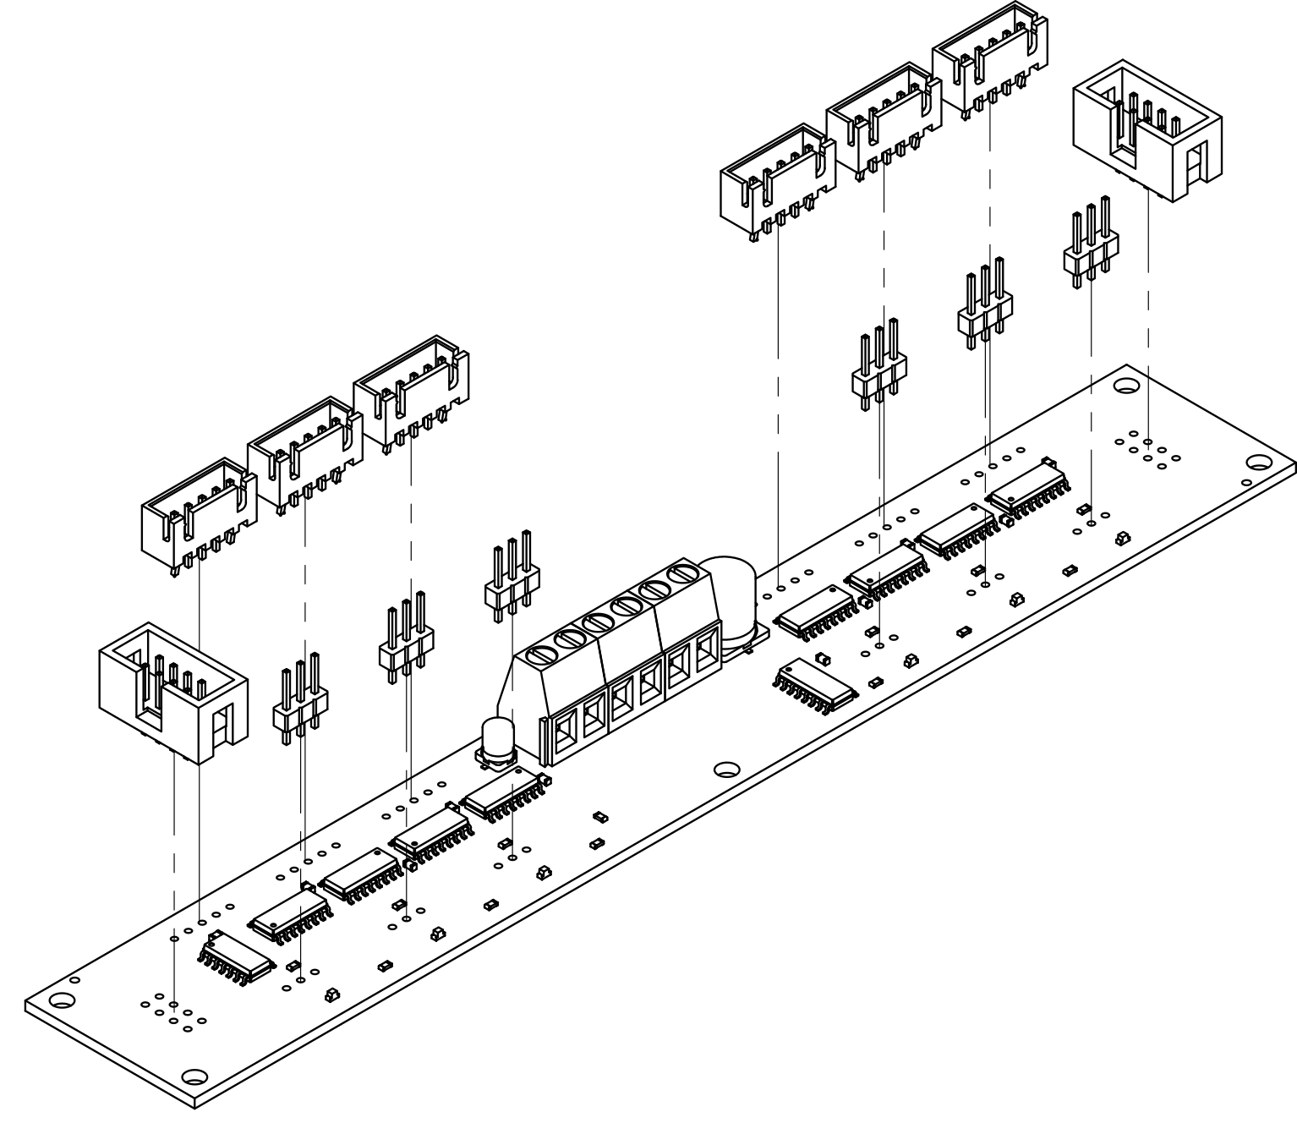
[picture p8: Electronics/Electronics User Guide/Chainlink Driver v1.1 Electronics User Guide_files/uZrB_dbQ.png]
User-uploaded image: chainlinkDrawing.png


- Insert the ribbon cable into a connector as shown, and gently clamp shut with a vise or pliers. Repeat with the other connector on the opposite end, making sure that both connectors face the same way - notches facing left.

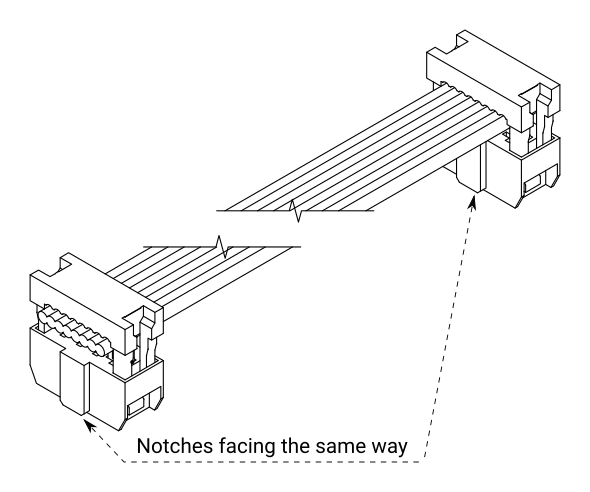
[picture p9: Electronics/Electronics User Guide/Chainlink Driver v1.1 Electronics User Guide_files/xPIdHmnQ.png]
User-uploaded image: ChainlinkCableIDCAssembly.png


- Not recommended, but you can optionally install the strain relief on the connectors (included with Bezek Labs Chainlink Driver boards): fold the ribbon cable back over the connector and install the plastic piece to clamp it down until it clicks. You’ll sacrifice some cable length and end up with a bulkier/taller connector, so I don’t think it’s worthwhile, especially since your cables shouldn’t be moving around much anyway.

# 3. Assemble the Chainlink Buddy

- Solder the connectors into place (make sure the IDC connector notch faces the left, as indicated on the PCB)

## T-Display Buddy

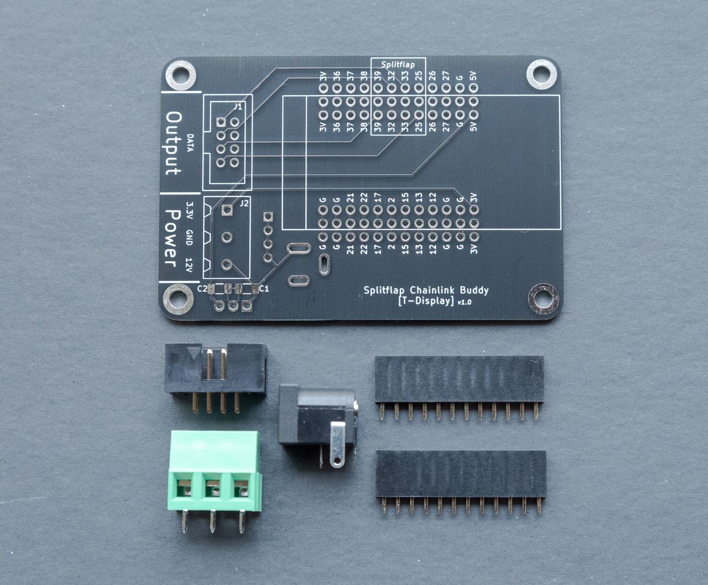
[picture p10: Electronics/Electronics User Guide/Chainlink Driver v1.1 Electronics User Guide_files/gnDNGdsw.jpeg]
User-uploaded image: DSC_5003_s.jpg


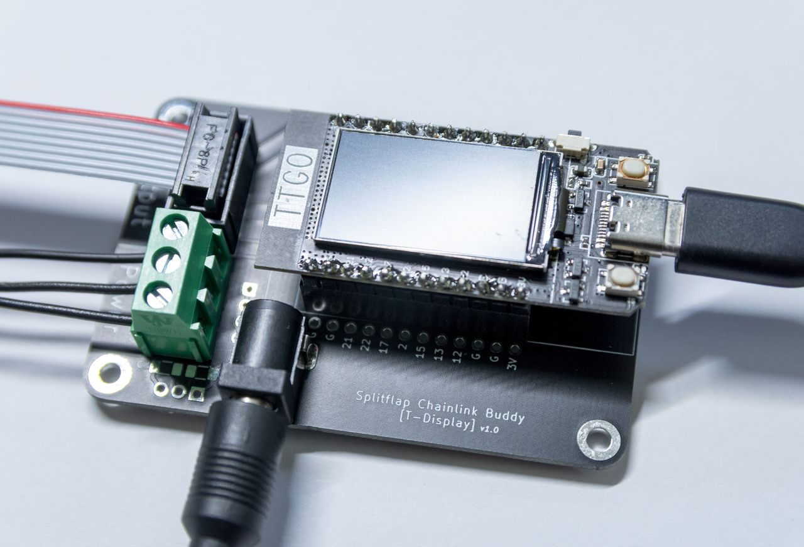
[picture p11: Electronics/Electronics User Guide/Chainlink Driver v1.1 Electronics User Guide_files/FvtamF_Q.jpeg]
User-uploaded image: DSC_5014_s.jpg


On the T-Display itself, you will solder the 2 rows of male headers (included in the box) to the T-Display, and then the whole module will plug into the matching female headers you soldered on the Buddy board.

You may notice a few empty spaces in the lower left of the T-Display Buddy PCB labeled C1 and C2 along with 3 through-holes; don’t worry, those are optional components and not needed for a basic setup. See Standalone T-Display operation (https://paper.dropbox.com/doc/Chainlink-Driver-v1.1-Electronics-User-Guide--BlREVjC8f3CL~b2gMbh4IclCAg-U0DAXrSxEoOhgSoRU39hq) for more info.

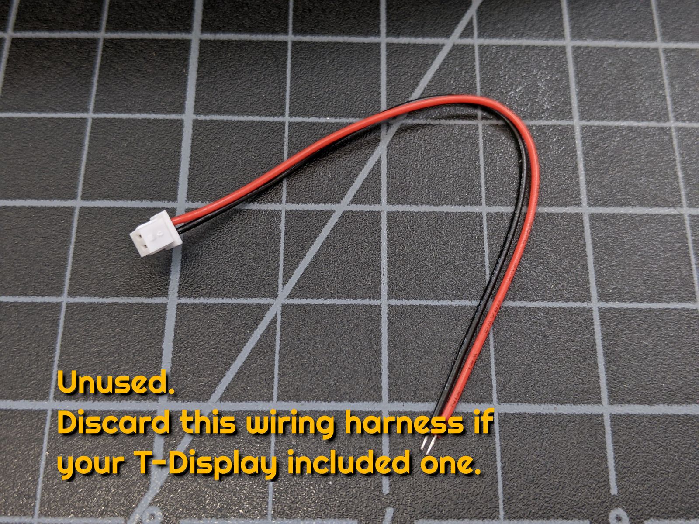
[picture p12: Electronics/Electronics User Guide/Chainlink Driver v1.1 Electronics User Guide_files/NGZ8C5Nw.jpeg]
User-uploaded image: PXL_20220317_223022886.jpg


Note: the T-Display often comes with a small Red/Black wiring harness with connector as well; it is unused with the Chainlink Buddy and can be discarded.

## Breadboard Buddy (alternative to T-Display Buddy)

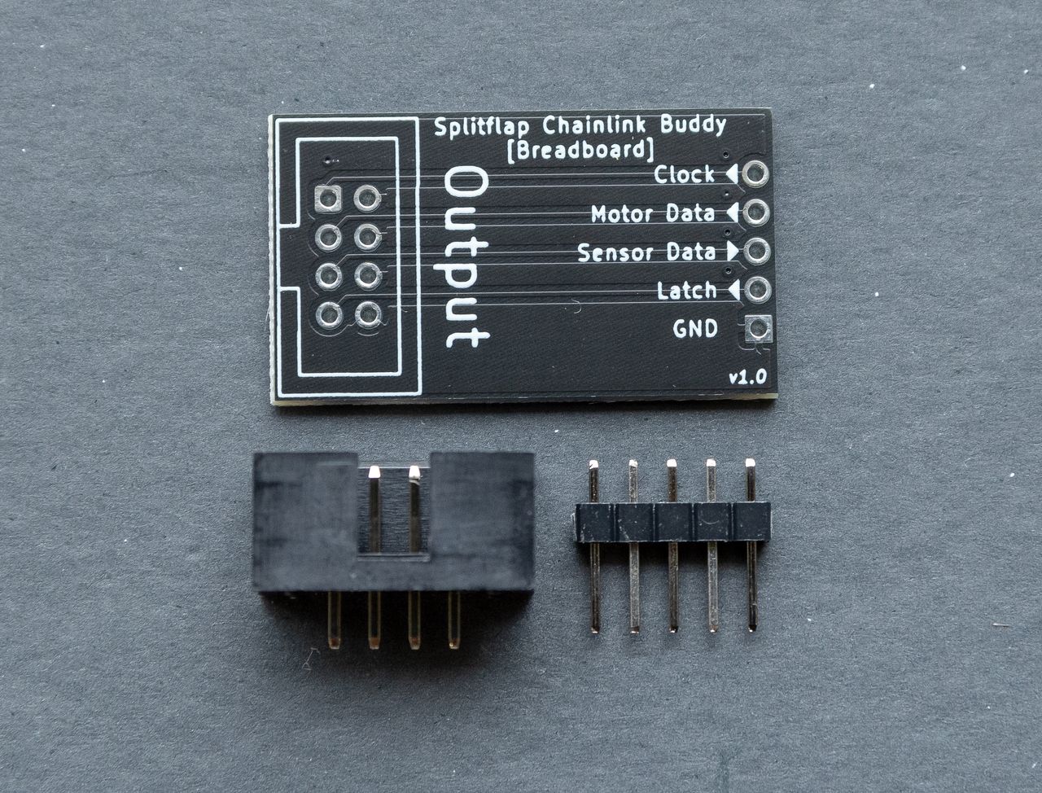
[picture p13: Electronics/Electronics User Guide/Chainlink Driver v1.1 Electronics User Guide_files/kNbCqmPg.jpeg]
User-uploaded image: DSC_5006.jpg


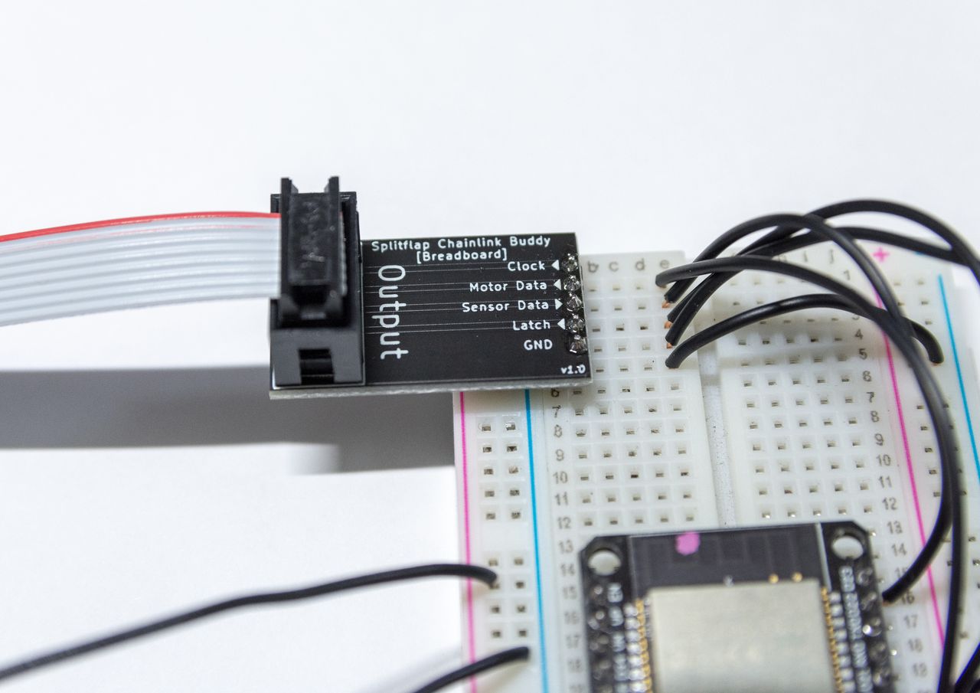
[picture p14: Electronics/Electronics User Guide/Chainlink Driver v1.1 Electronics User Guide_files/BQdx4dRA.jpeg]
User-uploaded image: DSC_5009_s.jpg


Alternatively: instead of the supplied IDC connector and a ribbon cable, you can install female headers (not included) on the bottom side of the PCB and plug the Buddy/breadboard into the Chainlink Driver directly with no cable:

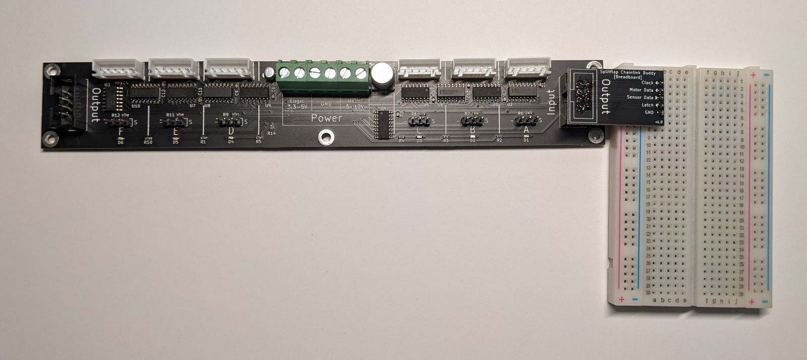
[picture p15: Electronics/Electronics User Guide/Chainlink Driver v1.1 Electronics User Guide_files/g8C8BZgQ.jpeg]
User-uploaded image: PXL_20211118_023229494.jpg


Alternative assembly of the Chainlink Buddy [Breadboard] using female headers (not included) to connect directly to the Chainlink Driver without a ribbon cable.

# 4. Connect Chainlink Driver to Chainlink Buddy

We’ll start by connecting and testing just the Chainlink Driver, without connecting a power supply or any modules’ motors or sensors. We’ll add those later, after confirming that the basic electronics work.

## T-Display

- Connect the ribbon cable from the Chainlink Buddy’s Output to the Chainlink Driver’s Input
- Connect a wire from the Chainlink Driver’s “Logic 3.3-5V” screw terminal to the “3.3V” screw terminal on the Chainlink Buddy
- Connect a wire from the Chainlink Driver’s “GND” screw terminal to the “GND” screw terminal on the Chainlink Buddy
- Connect a wire from the Chainlink Driver’s “Motor 5-12v” screw terminal to the “12V” screw terminal on the Chainlink Buddy
- ⚠️ Never connect a battery to the T-Display’s battery connector (small connector on the bottom of the TTGO T-Display module) when using the Chainlink Buddy!

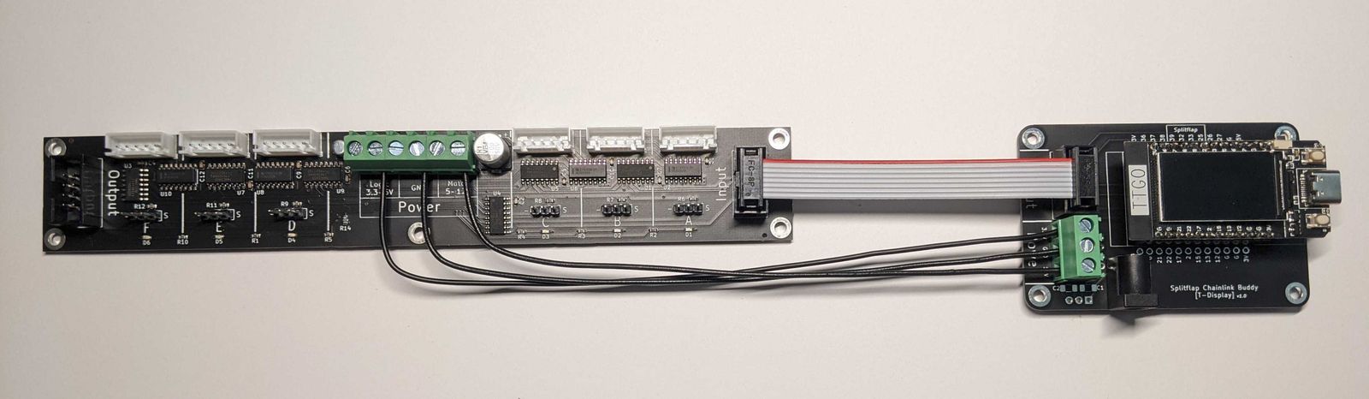
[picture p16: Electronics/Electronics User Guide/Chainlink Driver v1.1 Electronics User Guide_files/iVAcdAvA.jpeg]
User-uploaded image: PXL_20211118_023418663.jpg


## Breadboard (if you’re not using the T-Display Buddy)

- Connect the ribbon cable from the Chainlink Buddy’s Output to the Chainlink Driver’s Input
- Connect a wire from the Chainlink Driver’s “Logic 3.3-5V” screw terminal to a 3.3v supply on your breadboard
- Connect a wire from the Chainlink Driver’s “GND” screw terminal to your breadboard’s ground rail
- Connect the 5 pins to your ESP32. See the appendix (https://paper.dropbox.com/doc/Chainlink-Driver-v1.1-Electronics-User-Guide--BWhbqC5xa02TlskitjhIE95eAg-U0DAXrSxEoOhgSoRU39hq) for more info. Default pin assignments are:
- Clock: 33
- Motor Data: 32
- Sensor Data: 39
- Latch: 25
- GND: ground

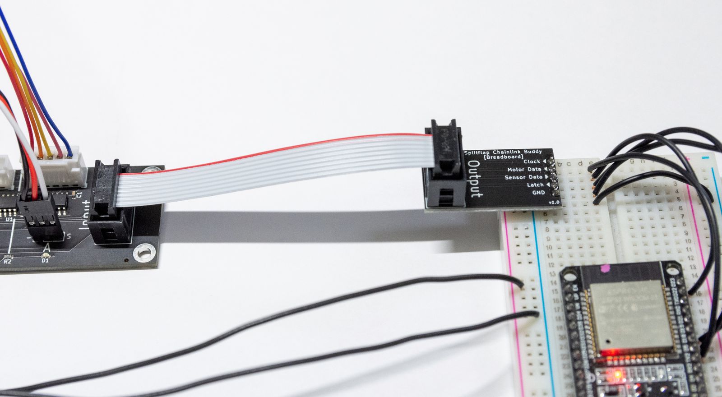
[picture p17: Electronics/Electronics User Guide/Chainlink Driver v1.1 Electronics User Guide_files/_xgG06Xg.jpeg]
User-uploaded image: DSC_5010.jpg


# 5. Install firmware

- Download and install Microsoft Visual Studio Code (https://code.visualstudio.com/)
- Follow these steps to set up Platform IO and the splitflap code:
- Install the Platform IO extension
- Choose “Clone Respository” in the Explorer sidebar and enter the git repo URL: https://github.com/scottbez1/splitflap.git
- Don’t open the repository directly in VS Code; instead, “Open Folder” and select the arduino/splitflap subfolder within the source folder you just cloned (if you open the root of the repo instead, Platform IO will not work)
- You may need to choose to “Trust” the folder to allow the Platform IO extension to run.

One of the benefits of Chainlink over the Classic Controller is that the firmware validates that the entire data chain is connected and working end-to-end (this is referred to as “loopback” checks), but to do so it needs to know how many Chainlink Driver boards to expect.

You’ll need to configure NUM_MODULES in platformio.ini to match the number of modules supported by the Chainlink Drivers you have connected. So for a single Chainlink Driver, set it to 6.

[env:chainlink]

extends=esp32base

build_flags =

${esp32base.build_flags}

-DCHAINLINK

-DNUM_MODULES=6

- (If you’re not using a T-Display, see the appendix (https://paper.dropbox.com/doc/Chainlink-Driver-v1.1-Electronics-User-Guide--BWhbqC5xa02TlskitjhIE95eAg-U0DAXrSxEoOhgSoRU39hq) for a few more changes you’ll need to make at this point)
- Mac Users: you will likely need to install updated drivers for the CH9102 USB-serial adapter used on newer versions of the ESP32 T-Display: https://learn.adafruit.com/how-to-install-drivers-for-wch-usb-to-serial-chips-ch9102f-ch9102/mac-driver-installation
- To upload code to the ESP32 T-Display from VS Code, you’ll need to (see screenshot below):
- 1) Open the Platform IO sidebar (click the alien icon on the left)
- 2) Click the “env” button at the bottom of the window and then in the dropdown at the top of the screen…
- 3) …select “env:chainlink” as the environment - this will set up code completion and syntax highlighting for the ESP32
- 4) in the Platform IO sidebar, expand the “General” section, and click Upload and Monitor

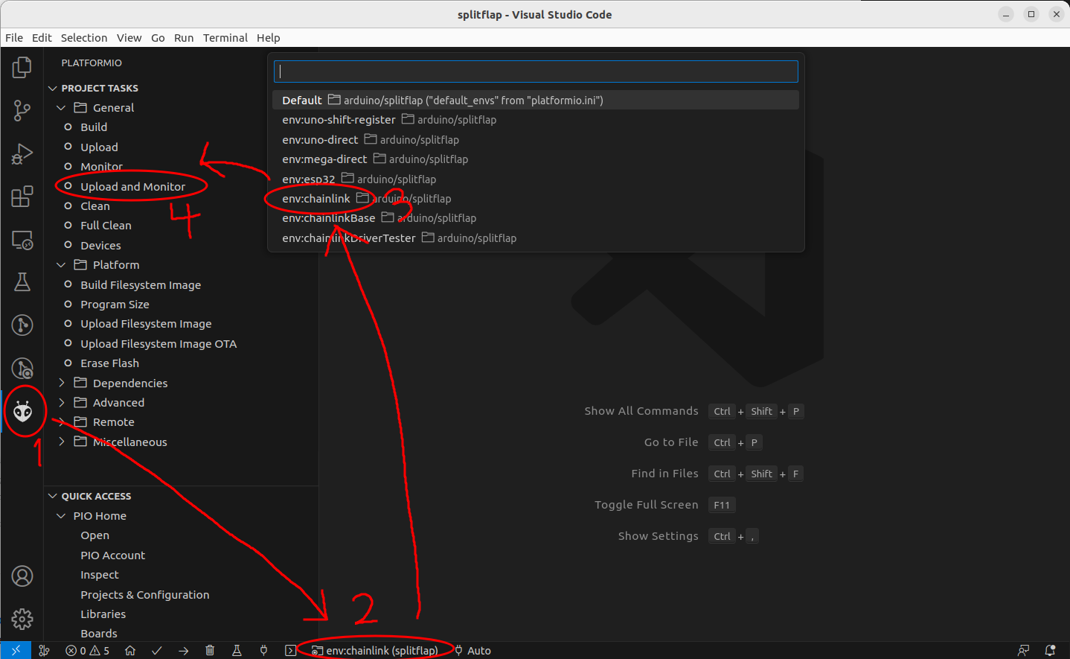
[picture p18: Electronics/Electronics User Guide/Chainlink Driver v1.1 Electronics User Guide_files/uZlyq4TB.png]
User-uploaded image: image.png


- If you reset the ESP32, you should see the LEDs on the Chainlink Drivers blink quickly and a message in the serial monitor that loopbacks are ok. If you see a loopback error message, troubleshoot that before continuing.

# 6. Connect modules and power

## Motors

- Plug into the white connectors. Note that module connections are laid out from right-to-left since the Chainlink Driver PCB is intended to sit behind the modules, so the first module plugs into position “A” on the right side of the PCB

## Sensors

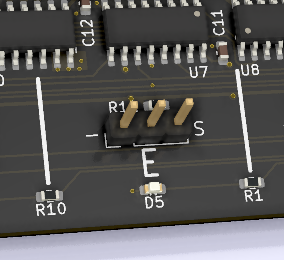
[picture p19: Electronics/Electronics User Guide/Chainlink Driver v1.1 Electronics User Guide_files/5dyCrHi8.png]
User-uploaded image: Screenshot+from+2021-07-29+17-38-43.png


- Plug sensor cable into corresponding 3-pin header
- Ground (black) should be on the left (toward the “Output” side), labeled “-”
- Signal (usually white) should be on the right (toward the “Input” side), labeled “S”

## Power

The ESP32 and 3.3v electronics on the Chainlink Drivers are typically powered by the USB connection to a computer. 12V power for the motors is supplied via a separate power supply.

- Note: never turn on 12V power when the ESP32 is not running! Doing so could damage your motors or worse.

T-Display

- You can plug a DC 12v barrel jack into the T-Display Buddy when using 1 or 2 Chainlink Drivers
- ⚠️ For more than 2 Chainlink Drivers, the barrel jack cannot handle enough current, so you should instead connect your power supply directly to the Motor Power terminals of the first Chainlink Driver. Make sure you are using the appropriate wire gauge (https://paper.dropbox.com/doc/Chainlink-Driver-v1.1-Electronics-User-Guide--BWhbqC5xa02TlskitjhIE95eAg-U0DAXrSxEoOhgSoRU39hq), and never chain power to more than 6 Chainlink Drivers (https://paper.dropbox.com/doc/Chainlink-Driver-v1.1-Electronics-User-Guide--BWhbqC5xa02TlskitjhIE95eAg-U0DAXrSxEoOhgSoRU39hq)

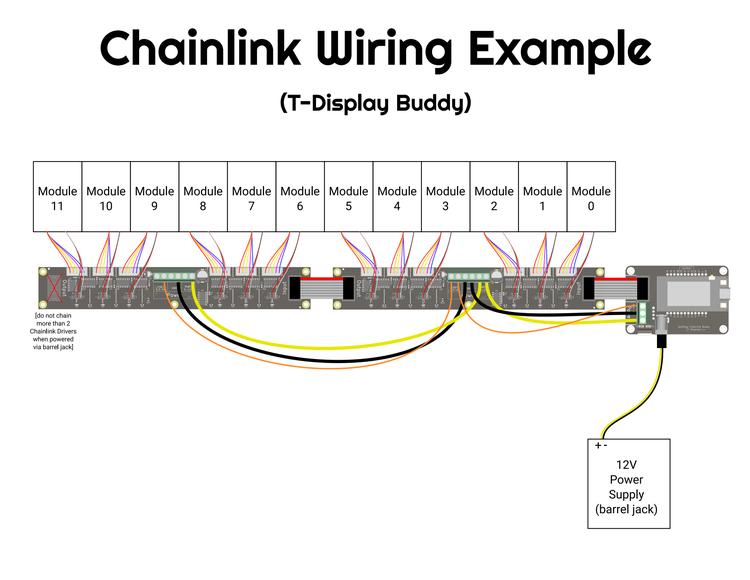
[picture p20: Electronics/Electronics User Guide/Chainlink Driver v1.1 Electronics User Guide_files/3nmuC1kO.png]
 (https://paper.dropbox.com/ep/redirect/external-link)

Dropbox file icon chainlinkBuddyWiringv1.1•PDF document

Breadboard

- Connect your power supply directly to the Motor Power terminals of the first Chainlink Driver. Make sure you are using the appropriate wire gauge (https://paper.dropbox.com/doc/Chainlink-Driver-v1.1-Electronics-User-Guide--BWhbqC5xa02TlskitjhIE95eAg-U0DAXrSxEoOhgSoRU39hq), and never chain power to more than 6 Chainlink Drivers (https://paper.dropbox.com/doc/Chainlink-Driver-v1.1-Electronics-User-Guide--BWhbqC5xa02TlskitjhIE95eAg-U0DAXrSxEoOhgSoRU39hq)

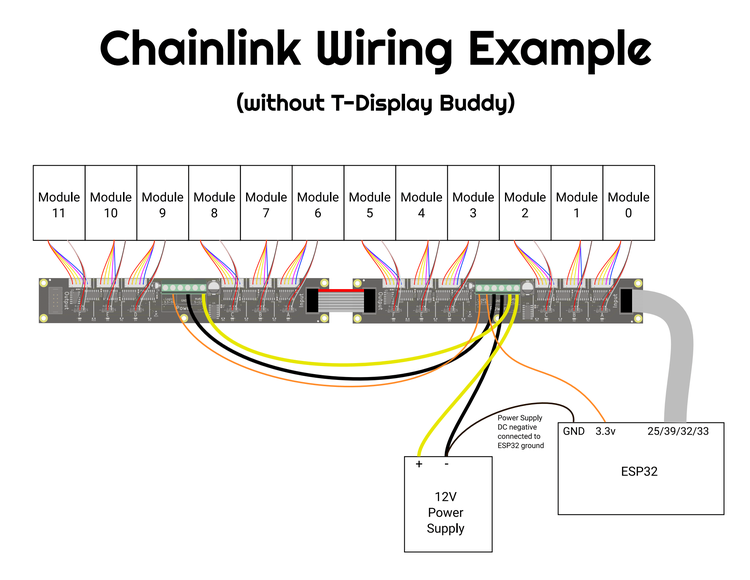
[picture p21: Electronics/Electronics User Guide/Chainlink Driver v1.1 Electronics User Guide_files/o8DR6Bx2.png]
 (https://paper.dropbox.com/ep/redirect/external-link)

Dropbox file icon chainlinkWiringv1.1 (1)•PDF document

# 7. (Optional) Adding more Drivers

You can easily chain several Chainlink Drivers by connecting ribbon cables, and adding additional power wires using the second set of power screw terminals (there are 2 terminals each for the 3.3v, ground, and 12v power), but make sure to follow this rule:

- ⚠️ Never chain power to more than 6 Chainlink Drivers in a row ⚠️

The screw terminals have a limited current rating (10A on the ones sold by Bezek Labs), so using more than 6 Chainlink Drivers will require power to be wired differently. See +Chainlink Driver v1.1 Electronics User Guide: Large-displays (https://paper.dropbox.com/doc/U0DAXrSxEoOhgSoRU39hq#:uid=280278286811718750760936&h2=Large-displays) below for more info on wiring large displays.

# 8. (Optional) Standalone T-Display operation

Under the normal configuration, you would power the motors with a 12V supply and separately the T-Display is powered via its 5V USB connection to a computer.

However, it’s possible to omit the USB connection for a completely standalone setup, powered by the 12V motor supply. This works well when you’re using the Wifi capabilities of the T-Display, for example to poll an HTTP(s) API or listen to an MQTT topic.

To do this, you’ll need to add 3 components to the Chainlink Buddy [T-Display] (must be purchased separately):

- 5V switching regulator
- Mornsun K7805-500R3 (https://www.digikey.com/en/products/detail/mornsun-america-llc/K7805-500R3/13168189) is one recommended option, but any switching regulator in a 7805 form-factor rated for 500mA+ should work - just double-check the capacitor requirements from the datasheet for the input (C1) and output (C2). A classic 7805 linear regulator is NOT recommended.
- 22uF 1206 ceramic capacitor - 16V - install to C2
- e.g. CL31A226MOCLNNC
- 10uF 1206 ceramic capacitor - 50V - install to C1
- e.g. CL31A106MBHNNNE (https://www.digikey.com/en/products/detail/samsung-electro-mechanics/CL31A106MBHNNNE/5961220)
- or just get 2 22uF capacitors and use for both C1 and C2, but make sure to choose one rated for 25V+, e.g. CL31A226KAHNNNE (https://www.digikey.com/en/products/detail/samsung-electro-mechanics/CL31A226KAHNNNE/3888705)

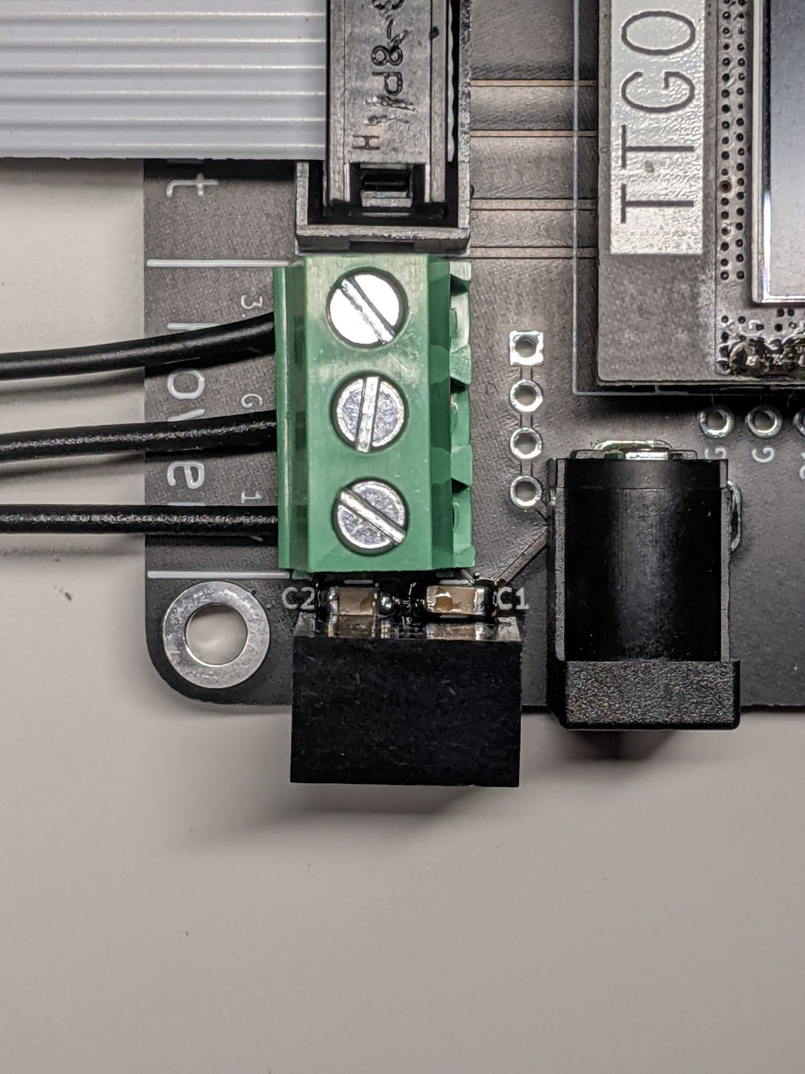
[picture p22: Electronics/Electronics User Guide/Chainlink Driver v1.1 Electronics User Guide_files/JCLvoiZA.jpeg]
User-uploaded image: 2021-12-10+16.26.37.jpg


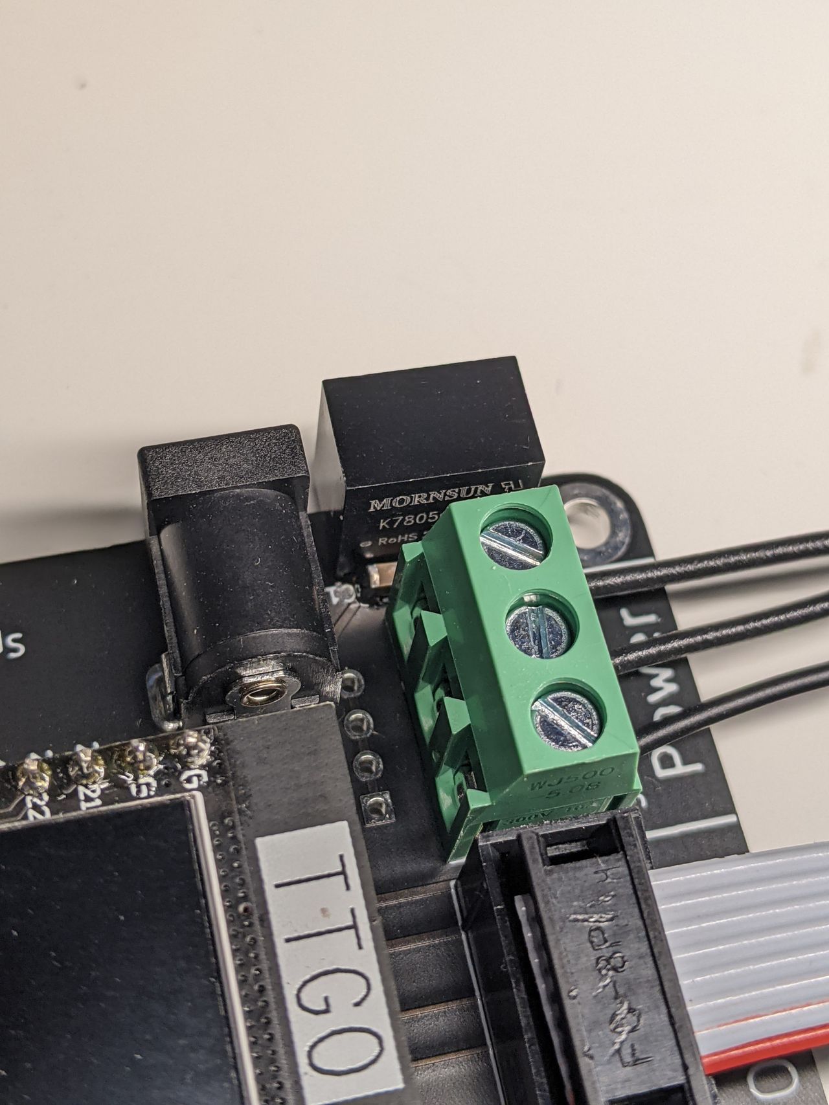
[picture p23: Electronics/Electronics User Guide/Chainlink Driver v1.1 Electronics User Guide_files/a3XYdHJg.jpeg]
User-uploaded image: 2021-12-10+16.28.06.jpg


# Appendix

## What is the Chainlink Driver?

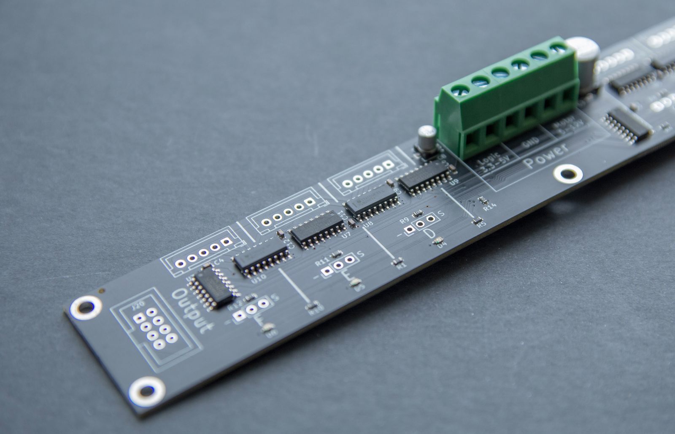
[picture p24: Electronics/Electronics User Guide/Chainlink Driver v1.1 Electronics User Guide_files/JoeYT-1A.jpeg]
User-uploaded image: DSC_4991_s.jpg


The Chainlink Driver is an updated control board for splitflap displays, building on lessons learned from the Classic Controller.

There were 2 main goals in designing it:

- support for controlling a LOT of splitflaps
- low cost and ease of purchasing pre-assembled boards - it’s mostly SMD instead of through-hole

Each Chainlink Driver PCBA contains all the power and signal electronics to drive the stepper motors and read the home position sensors for up to six modules, and can be trivially chained together to control 100+ splitflap modules using just 4 pins of an ESP32.

(https://paper.dropbox.com/ep/redirect/external-link?url=https%3A%2F%2Fyoutu.be%2Fg9EPabcxBsM)

This 108-module display is driven by a single TTGO T-Display microcontroller and 18 Chainlink Driver boards.

## Where to buy a Chainlink Driver?

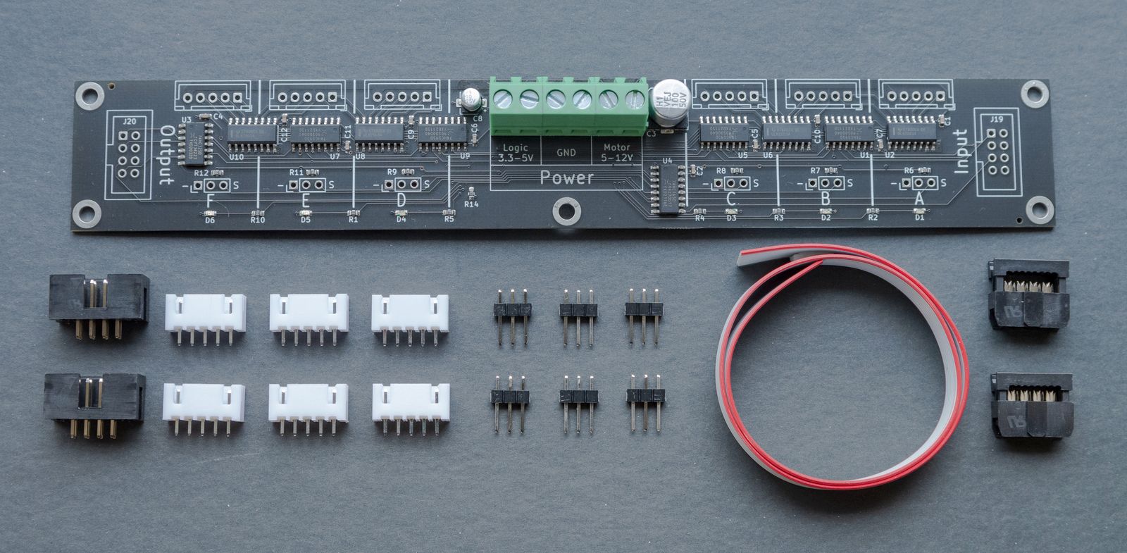
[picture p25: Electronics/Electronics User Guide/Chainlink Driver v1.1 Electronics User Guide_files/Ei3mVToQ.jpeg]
User-uploaded image: DSC_4994_s.jpg


The design is open source, so you can order them directly from a PCB manufacturer using the design files provided, but I also sell them in my Bezek Labs Etsy store (https://www.etsy.com/listing/1123280069/splitflap-chainlink-driver-v11) within the US.

Buying them from my store has the advantage of being 100% functionality tested after assembly using a custom testbed (https://twitter.com/scottbez1/status/1414986069586575360), and it helps support further development and prototyping of this project. I also include all the connectors and a ribbon cable for your convenience.

If you’d like to order them directly from a PCB manufacturer, the designs are optimized for JLCPCB’s Assembly service (not sponsored or affiliated, but they do have extremely cheap assembly as long as you stick to a limited set of components available in their part library). Note that the BOM does not include many of the connectors because there is a $3-per-unique-part fee, and since you’ll need to order the ribbon cable separately anyway this can keep your costs lower for small orders.

## Power supply tips

You’ll need a 12V supply with a current rating that depends on the number of modules you’ll be controlling (and even the particular motors you’re using, as not all 28byj-48 motors have the same coil resistance).

A good starting assumption is that each motor will draw 0.25A each (typical estimate for motors with 100 ohm half-winding resistance), but you should always test your motors, and include a safety margin.

So for every Chainlink Driver you use, plan for at least 1.25A capacity, but many cheap power supplies have questionable/overstated ratings, so you probably want 2A minimum.

For a large display, I’ve used a Mean Well LRS-350-12 (https://amzn.to/3cdjuwD) [affiliate links help support this project at no cost to you, or use a non-affiliate link (https://www.amazon.com/MEAN-WELL-LRS-350-12-Computer-Project/dp/B07VTLJS18) if you’d prefer] which I found to easily supply 22+ amps with little voltage ripple.

Make sure to select appropriate gauge copper wire for power (this includes the GND wires!). The current along a chain of Chainlink Driver boards adds up quickly!

I also recommend adding fuses near the power supply as an added layer of protection, especially on larger displays. The LRS-350-12 mentioned above is capable of supplying 29A continuously which is a lot of current and potentially destructive in case of a fault. Since each power branch (see advanced wiring diagram) will use less than this, you should protect each branch with its own appropriately-sized fuse.

Make sure to buy power wiring from a reputable seller with a trustworthy supply chain (e.g. an electronics supplier or a big box hardware store, not AliExpress or Amazon). Unfortunately, as the cost of copper has gone up it’s more common to find wire using other metals which may not meet its advertised specs.

## Using a different ESP32 module

In theory, any ESP32 module with 2 cores (i.e. not based on an ESP32-S2) should work. Most common WROOM or WROVER-based modules can work.

However, not all cheap modules are well designed (some are not breadboard friendly, some have poor power design causing brownouts during wifi/ble, etc), so I’ve found the T-Display to be a great default. You do lose a few IO pins to the LCD, but the Chainlink firmware supports the LCD out of the box and I think you’ll find it handy for debugging.

That said, if you do use another module here’s what you need to know:

1. You probably want to disable the display code to free up those pins and avoid wasting CPU cycles. Do this by changing -DENABLE_DISPLAY=1 to -DENABLE_DISPLAY=0 in platformio.ini
2. Since the ESP32 has a GPIO matrix, you can change the pin assignments easily (see spi_io_config.h), but you do need to avoid certain reserved functions (https://www.youtube.com/watch?v=LY-1DHTxRAk) so I recommend using the defaults unless you have a good reason not to.

## Large displays

The Chainlink system can support large displays, but please be aware that more care needs to be taken as the size of the display (and therefore, the power supply and electronics involved) increases.

If you are wiring more than 6 Chainlink Driver boards, only data connections should form a continuous chain! This is shown in blue on the diagram below.

The power should branch into separate chains of up to 6 Drivers (or fewer if your motors require more current).

Chaining power continuously like the data would overload the screw terminals and wires at the beginning of the chain, potentially causing damage/fire. Note how the yellow and black wires in the diagram below branch at the power supply and do not continue past each sub-chain of 6 Drivers.

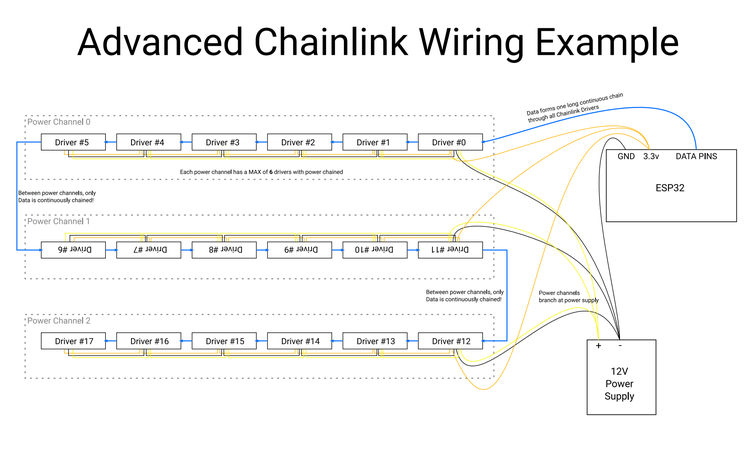
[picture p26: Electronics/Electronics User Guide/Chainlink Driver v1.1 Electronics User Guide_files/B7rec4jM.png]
 (https://paper.dropbox.com/ep/redirect/external-link)

Dropbox file icon chainlinkWiringAdvanced•PDF document

I would also strongly recommend adding additional safety measures with a display of this size, considering the total power involved. For instance:

- Fuses for each branch of power
- Real-time voltage & current monitoring, and individual load switches for each “branch” to detect and respond to faults
- Relay controlling mains input to 12V power supply (intentionally redundant with 12V branch load switches)

The Chainlink Base (taking the place of the Chainlink Buddy in the system) is one possible approach to some of these measures, but it is not officially supported/recommended.

Make sure you consult a qualified electrician/engineer to review all designs (including splitflap project schematics and PCBs), and be sure to follow applicable regulatory codes.

- Chainlink Driver v1.1 Electronics User Guide (https://paper.dropbox.com/doc/Chainlink-Driver-v1.1-Electronics-User-Guide-U0DAXrSxEoOhgSoRU39hq)
- Intro (https://paper.dropbox.com/doc/Chainlink-Driver-v1.1-Electronics-User-Guide-U0DAXrSxEoOhgSoRU39hq)
- 1. Gather the parts (https://paper.dropbox.com/doc/Chainlink-Driver-v1.1-Electronics-User-Guide-U0DAXrSxEoOhgSoRU39hq)
- 2. Finish assembling the PCB (https://paper.dropbox.com/doc/Chainlink-Driver-v1.1-Electronics-User-Guide-U0DAXrSxEoOhgSoRU39hq)
- 3. Assemble the Chainlink Buddy (https://paper.dropbox.com/doc/Chainlink-Driver-v1.1-Electronics-User-Guide-U0DAXrSxEoOhgSoRU39hq)
- T-Display Buddy (https://paper.dropbox.com/doc/Chainlink-Driver-v1.1-Electronics-User-Guide-U0DAXrSxEoOhgSoRU39hq)
- Breadboard Buddy (alternative to T-Display Buddy) (https://paper.dropbox.com/doc/Chainlink-Driver-v1.1-Electronics-User-Guide-U0DAXrSxEoOhgSoRU39hq)
- 4. Connect Chainlink Driver to Chainlink Buddy (https://paper.dropbox.com/doc/Chainlink-Driver-v1.1-Electronics-User-Guide-U0DAXrSxEoOhgSoRU39hq)
- T-Display (https://paper.dropbox.com/doc/Chainlink-Driver-v1.1-Electronics-User-Guide-U0DAXrSxEoOhgSoRU39hq)
- Breadboard (if you’re not using the T-Display Buddy) (https://paper.dropbox.com/doc/Chainlink-Driver-v1.1-Electronics-User-Guide-U0DAXrSxEoOhgSoRU39hq)
- 5. Install firmware (https://paper.dropbox.com/doc/Chainlink-Driver-v1.1-Electronics-User-Guide-U0DAXrSxEoOhgSoRU39hq)
- 6. Connect modules and power (https://paper.dropbox.com/doc/Chainlink-Driver-v1.1-Electronics-User-Guide-U0DAXrSxEoOhgSoRU39hq)
- Motors (https://paper.dropbox.com/doc/Chainlink-Driver-v1.1-Electronics-User-Guide-U0DAXrSxEoOhgSoRU39hq)
- Sensors (https://paper.dropbox.com/doc/Chainlink-Driver-v1.1-Electronics-User-Guide-U0DAXrSxEoOhgSoRU39hq)
- Power (https://paper.dropbox.com/doc/Chainlink-Driver-v1.1-Electronics-User-Guide-U0DAXrSxEoOhgSoRU39hq)
- T-Display (https://paper.dropbox.com/doc/Chainlink-Driver-v1.1-Electronics-User-Guide-U0DAXrSxEoOhgSoRU39hq)
- Breadboard (https://paper.dropbox.com/doc/Chainlink-Driver-v1.1-Electronics-User-Guide-U0DAXrSxEoOhgSoRU39hq)
- 7. (Optional) Adding more Drivers (https://paper.dropbox.com/doc/Chainlink-Driver-v1.1-Electronics-User-Guide-U0DAXrSxEoOhgSoRU39hq)
- 8. (Optional) Standalone T-Display operation (https://paper.dropbox.com/doc/Chainlink-Driver-v1.1-Electronics-User-Guide-U0DAXrSxEoOhgSoRU39hq)
- Appendix (https://paper.dropbox.com/doc/Chainlink-Driver-v1.1-Electronics-User-Guide-U0DAXrSxEoOhgSoRU39hq)
- What is the Chainlink Driver? (https://paper.dropbox.com/doc/Chainlink-Driver-v1.1-Electronics-User-Guide-U0DAXrSxEoOhgSoRU39hq)
- Where to buy a Chainlink Driver? (https://paper.dropbox.com/doc/Chainlink-Driver-v1.1-Electronics-User-Guide-U0DAXrSxEoOhgSoRU39hq)
- Power supply tips (https://paper.dropbox.com/doc/Chainlink-Driver-v1.1-Electronics-User-Guide-U0DAXrSxEoOhgSoRU39hq)
- Using a different ESP32 module (https://paper.dropbox.com/doc/Chainlink-Driver-v1.1-Electronics-User-Guide-U0DAXrSxEoOhgSoRU39hq)
- Large displays (https://paper.dropbox.com/doc/Chainlink-Driver-v1.1-Electronics-User-Guide-U0DAXrSxEoOhgSoRU39hq)

Updated 65 days ago

## Emoji

raised hand

- raised hand: light skin tone
- raised hand: medium-light skin tone
- raised hand: medium skin tone
- raised hand: medium-dark skin tone
- raised hand: dark skin tone
- raised hand

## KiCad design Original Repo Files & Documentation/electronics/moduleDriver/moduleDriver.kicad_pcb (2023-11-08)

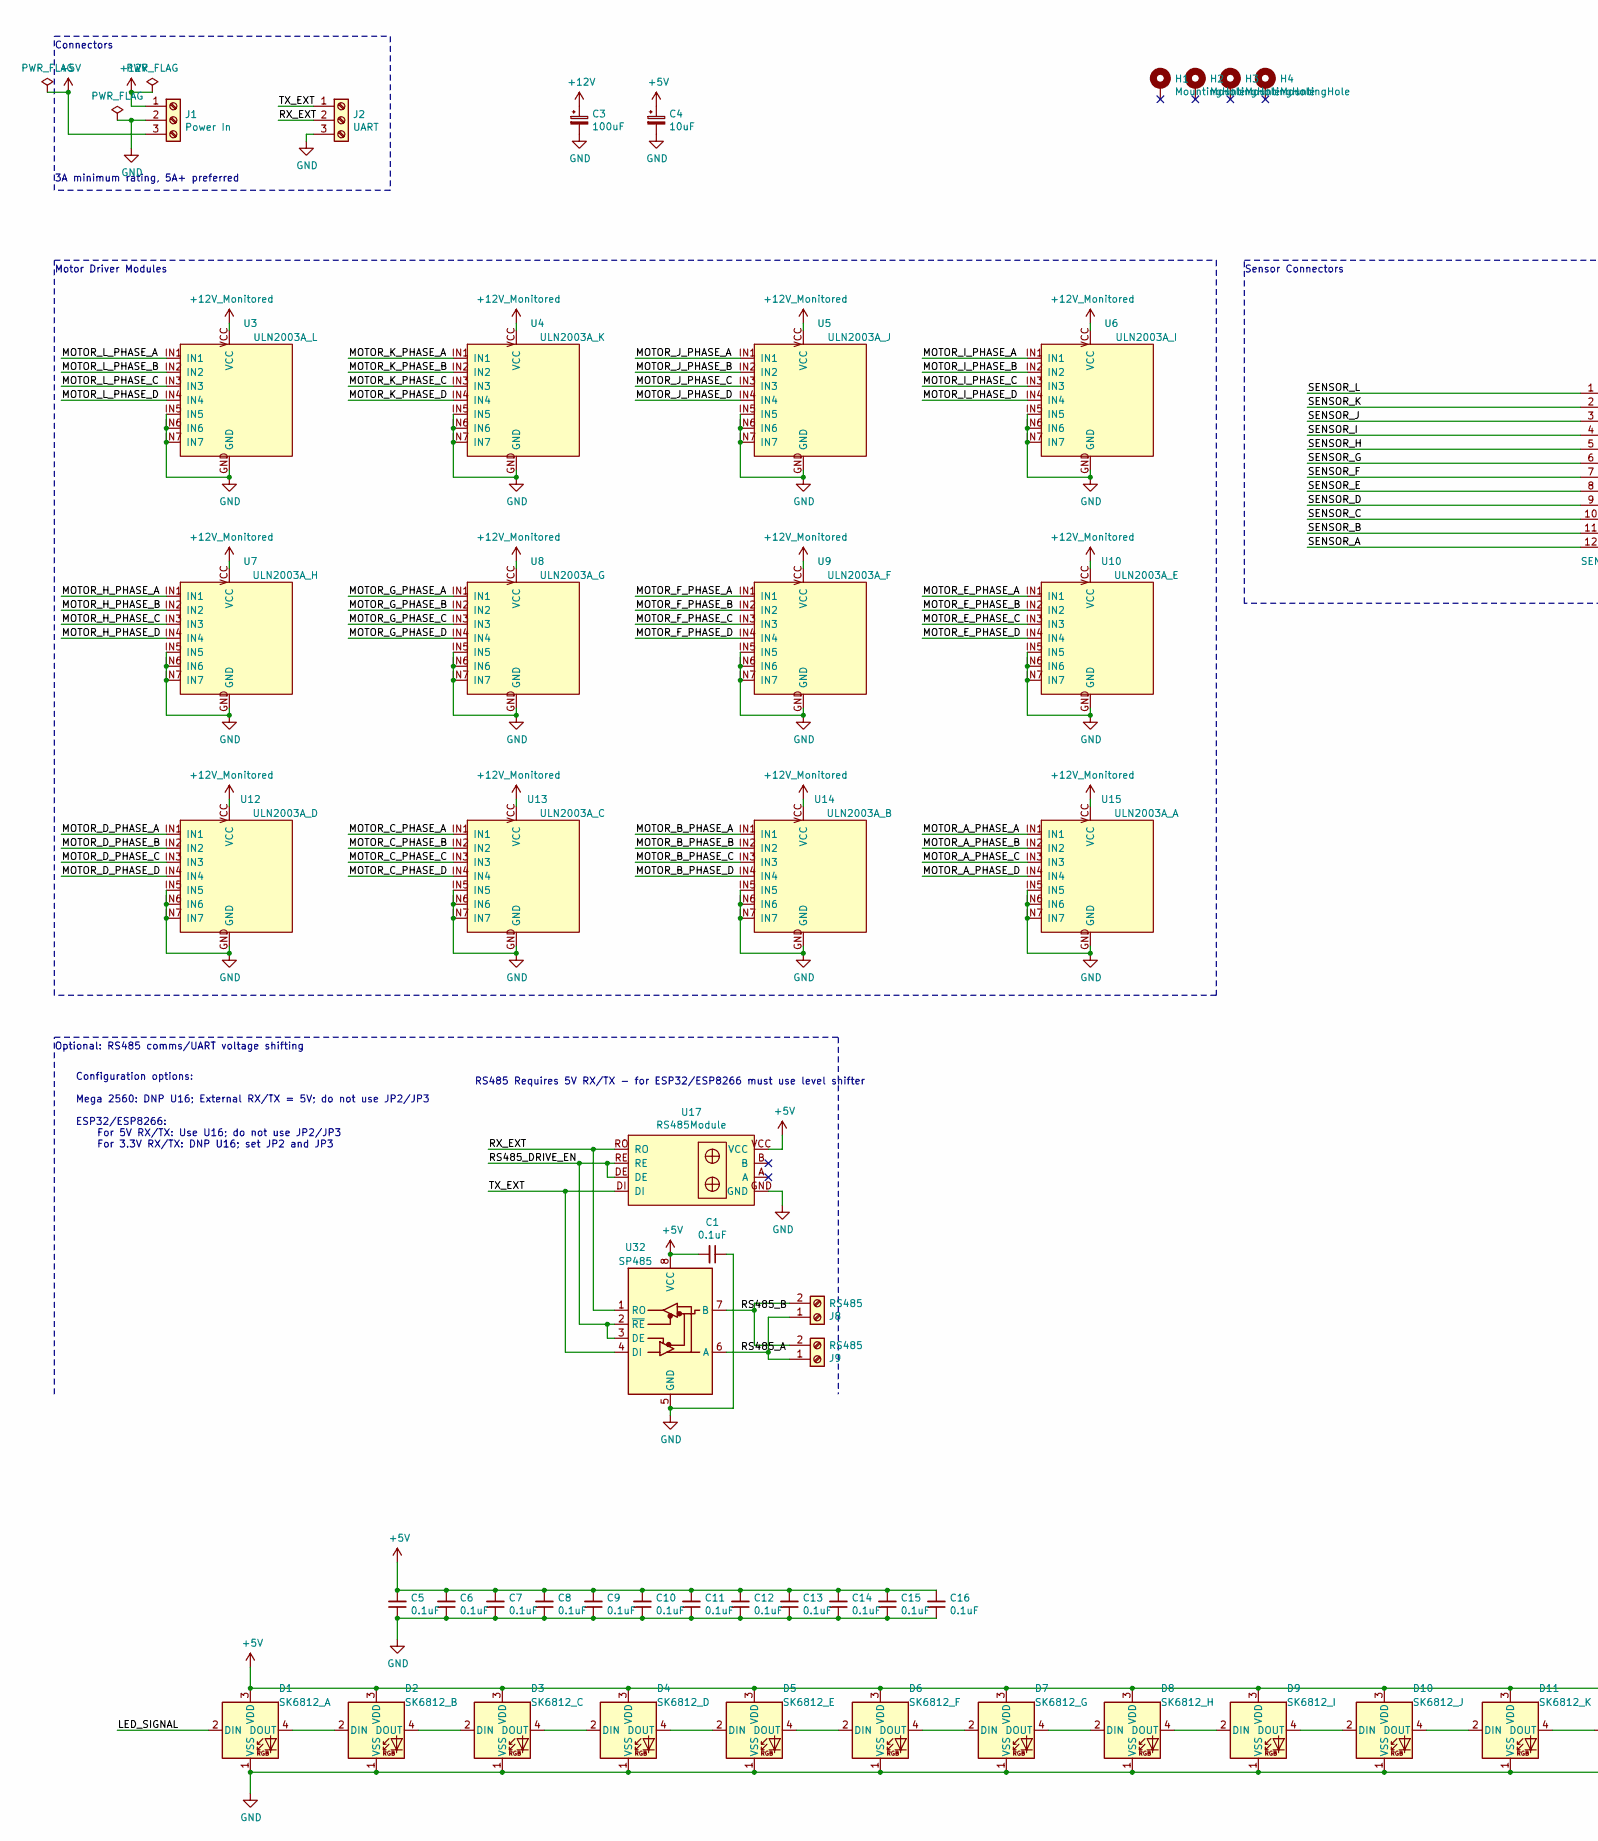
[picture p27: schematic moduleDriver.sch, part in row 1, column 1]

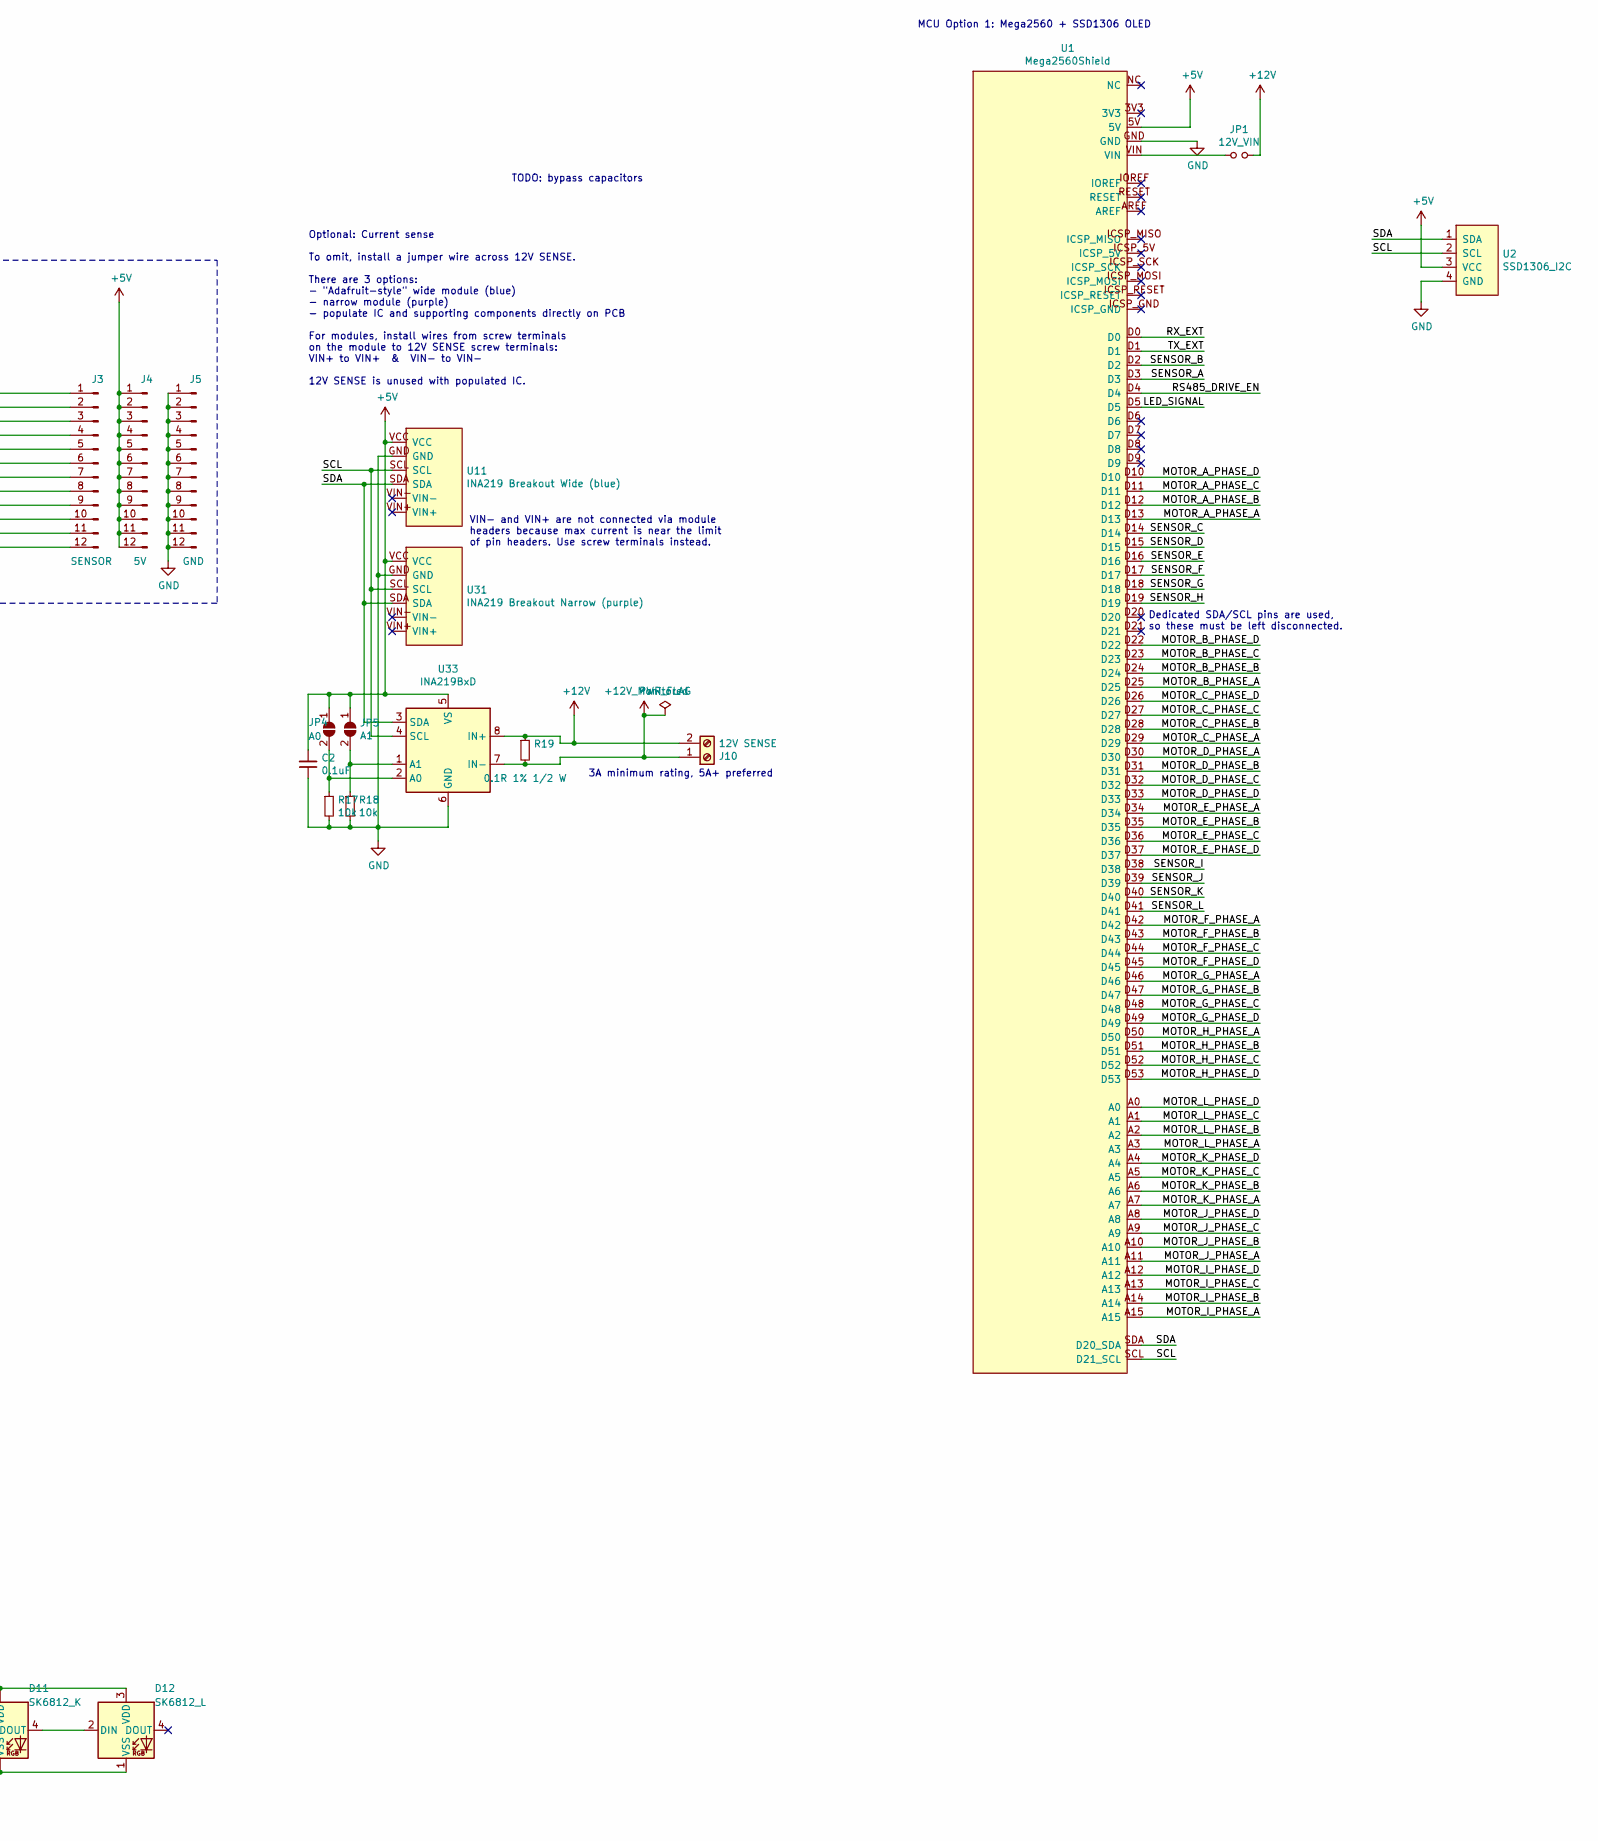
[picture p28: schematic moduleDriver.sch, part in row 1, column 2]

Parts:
C1, C2, C5, C6, C7, C8, C9, C10, C11, C12, C13, C14, C15, C16: 0.1uF; C_0805_2012Metric_Pad1.15x1.40mm_HandSolder
C3: 100uF; CP_Radial_D10.0mm_P3.50mm
C4: 10uF; CP_Radial_D6.3mm_P2.50mm
D1: SK6812_A; LED_SK6812_PLCC4_5.0x5.0mm_P3.2mm
D2: SK6812_B; LED_SK6812_PLCC4_5.0x5.0mm_P3.2mm
D3: SK6812_C; LED_SK6812_PLCC4_5.0x5.0mm_P3.2mm
D4: SK6812_D; LED_SK6812_PLCC4_5.0x5.0mm_P3.2mm
D5: SK6812_E; LED_SK6812_PLCC4_5.0x5.0mm_P3.2mm
D6: SK6812_F; LED_SK6812_PLCC4_5.0x5.0mm_P3.2mm
D7: SK6812_G; LED_SK6812_PLCC4_5.0x5.0mm_P3.2mm
D8: SK6812_H; LED_SK6812_PLCC4_5.0x5.0mm_P3.2mm
D9: SK6812_I; LED_SK6812_PLCC4_5.0x5.0mm_P3.2mm
D10: SK6812_J; LED_SK6812_PLCC4_5.0x5.0mm_P3.2mm
D11: SK6812_K; LED_SK6812_PLCC4_5.0x5.0mm_P3.2mm
D12: SK6812_L; LED_SK6812_PLCC4_5.0x5.0mm_P3.2mm
H1, H2, H3, H4: MountingHole; MountingHole_4.3mm_M4_ISO7380_Pad
J1: Power In; TerminalBlock_bornier-3_P5.08mm
J2: UART; TerminalBlock_bornier-3_P5.08mm
J3: SENSOR; PinHeader_1x12_P2.54mm_Vertical
J4: 5V; PinHeader_1x12_P2.54mm_Vertical
J5: GND; PinHeader_1x12_P2.54mm_Vertical
J8, J9: RS485; TerminalBlock_bornier-2_P5.08mm
J10: 12V SENSE; TerminalBlock_bornier-2_P5.08mm
JP1: 12V_VIN; PinHeader_1x02_P2.54mm_Vertical
JP4: A0; SolderJumper-2_P1.3mm_Open_TrianglePad1.0x1.5mm
JP5: A1; SolderJumper-2_P1.3mm_Open_TrianglePad1.0x1.5mm
R17, R18: 10k; R_0805_2012Metric_Pad1.15x1.40mm_HandSolder
R19: 0.1R 1% 1/2 W; R_2512_6332Metric_Pad1.52x3.35mm_HandSolder
U1: Mega2560Shield; Mega2560Shield_Modified
U2: SSD1306_I2C; SSD1306_128x32
U3: ULN2003A_L; ULN2003AModule_No_EN_No_FSilk
U4: ULN2003A_K; ULN2003AModule_No_EN_No_FSilk
U5: ULN2003A_J; ULN2003AModule_No_EN_No_FSilk
U6: ULN2003A_I; ULN2003AModule_No_EN_No_FSilk
U7: ULN2003A_H; ULN2003AModule_No_EN_No_FSilk
U8: ULN2003A_G; ULN2003AModule_No_EN_No_FSilk
U9: ULN2003A_F; ULN2003AModule_No_EN_No_FSilk
U10: ULN2003A_E; ULN2003AModule_No_EN_No_FSilk
U11: INA219 Breakout Wide (blue); INA219_LARGE
U12: ULN2003A_D; ULN2003AModule_No_EN_No_FSilk
U13: ULN2003A_C; ULN2003AModule_No_EN_No_FSilk
U14: ULN2003A_B; ULN2003AModule_No_EN_No_FSilk
U15: ULN2003A_A; ULN2003AModule_No_EN_No_FSilk
U17: RS485Module
U31: INA219 Breakout Narrow (purple); INA219_SMALL
U32: SP485; SOIC-8_3.9x4.9mm_P1.27mm
U33: INA219BxD; SOIC-8_3.9x4.9mm_P1.27mm

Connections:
+5V: C1.2, C2.2, C4.1, C5.2, C6.2, C7.2, C8.2, C9.2, C10.2, C11.2, C12.2, C13.2, C14.2, C15.2, C16.2, D1.3 (VDD), D2.3 (VDD), D3.3 (VDD), D4.3 (VDD), D5.3 (VDD), D6.3 (VDD), D7.3 (VDD), D8.3 (VDD), D9.3 (VDD), D10.3 (VDD), D11.3 (VDD), D12.3 (VDD), J1.3, J4.1, J4.2, J4.3, J4.4, J4.5, J4.6, J4.7, J4.8, J4.9, J4.10, J4.11, J4.12, JP4.1 (A), JP5.1 (A), U1.5V, U2.3 (VCC), U11.VCC, U17.VCC, U31.VCC, U32.8 (VCC), U33.5 (VS)
+12V: C3.1, J1.1, J10.2, JP1.2, R19.1, U33.8 (IN+)
+12V_Monitored: J10.1, R19.2, U3.VCC, U4.VCC, U5.VCC, U6.VCC, U7.VCC, U8.VCC, U9.VCC, U10.VCC, U12.VCC, U13.VCC, U14.VCC, U15.VCC, U33.7 (IN-)
/LED_SIGNAL: D1.2 (DIN), U1.D5
/MOTOR_A_PHASE_A: U1.D13, U15.IN1
/MOTOR_A_PHASE_B: U1.D12, U15.IN2
/MOTOR_A_PHASE_C: U1.D11, U15.IN3
/MOTOR_A_PHASE_D: U1.D10, U15.IN4
/MOTOR_B_PHASE_A: U1.D25, U14.IN1
/MOTOR_B_PHASE_B: U1.D24, U14.IN2
/MOTOR_B_PHASE_C: U1.D23, U14.IN3
/MOTOR_B_PHASE_D: U1.D22, U14.IN4
/MOTOR_C_PHASE_A: U1.D29, U13.IN1
/MOTOR_C_PHASE_B: U1.D28, U13.IN2
/MOTOR_C_PHASE_C: U1.D27, U13.IN3
/MOTOR_C_PHASE_D: U1.D26, U13.IN4
/MOTOR_D_PHASE_A: U1.D30, U12.IN1
/MOTOR_D_PHASE_B: U1.D31, U12.IN2
/MOTOR_D_PHASE_C: U1.D32, U12.IN3
/MOTOR_D_PHASE_D: U1.D33, U12.IN4
/MOTOR_E_PHASE_A: U1.D34, U10.IN1
/MOTOR_E_PHASE_B: U1.D35, U10.IN2
/MOTOR_E_PHASE_C: U1.D36, U10.IN3
/MOTOR_E_PHASE_D: U1.D37, U10.IN4
/MOTOR_F_PHASE_A: U1.D42, U9.IN1
/MOTOR_F_PHASE_B: U1.D43, U9.IN2
/MOTOR_F_PHASE_C: U1.D44, U9.IN3
/MOTOR_F_PHASE_D: U1.D45, U9.IN4
/MOTOR_G_PHASE_A: U1.D46, U8.IN1
/MOTOR_G_PHASE_B: U1.D47, U8.IN2
/MOTOR_G_PHASE_C: U1.D48, U8.IN3
/MOTOR_G_PHASE_D: U1.D49, U8.IN4
/MOTOR_H_PHASE_A: U1.D50, U7.IN1
/MOTOR_H_PHASE_B: U1.D51, U7.IN2
/MOTOR_H_PHASE_C: U1.D52, U7.IN3
/MOTOR_H_PHASE_D: U1.D53, U7.IN4
/MOTOR_I_PHASE_A: U1.A15, U6.IN1
/MOTOR_I_PHASE_B: U1.A14, U6.IN2
/MOTOR_I_PHASE_C: U1.A13, U6.IN3
/MOTOR_I_PHASE_D: U1.A12, U6.IN4
/MOTOR_J_PHASE_A: U1.A11, U5.IN1
/MOTOR_J_PHASE_B: U1.A10, U5.IN2
/MOTOR_J_PHASE_C: U1.A9, U5.IN3
/MOTOR_J_PHASE_D: U1.A8, U5.IN4
/MOTOR_K_PHASE_A: U1.A7, U4.IN1
/MOTOR_K_PHASE_B: U1.A6, U4.IN2
/MOTOR_K_PHASE_C: U1.A5, U4.IN3
/MOTOR_K_PHASE_D: U1.A4, U4.IN4
/MOTOR_L_PHASE_A: U1.A3, U3.IN1
/MOTOR_L_PHASE_B: U1.A2, U3.IN2
/MOTOR_L_PHASE_C: U1.A1, U3.IN3
/MOTOR_L_PHASE_D: U1.A0, U3.IN4
/RS485_A: J8.1, J9.1, U32.6 (A)
/RS485_B: J8.2, J9.2, U32.7 (B)
/RS485_DRIVE_EN: U1.D4, U17.DE, U17.RE, U32.2 (~RE), U32.3 (DE)
/RX_EXT: J2.2, U1.D0, U17.RO, U32.1 (RO)
/SCL: U1.SCL (D21_SCL), U2.2 (SCL), U11.SCL, U31.SCL, U33.4 (SCL)
/SDA: U1.SDA (D20_SDA), U2.1 (SDA), U11.SDA, U31.SDA, U33.3 (SDA)
/SENSOR_A: J3.12, U1.D3
/SENSOR_B: J3.11, U1.D2
/SENSOR_C: J3.10, U1.D14
/SENSOR_D: J3.9, U1.D15
/SENSOR_E: J3.8, U1.D16
/SENSOR_F: J3.7, U1.D17
/SENSOR_G: J3.6, U1.D18
/SENSOR_H: J3.5, U1.D19
/SENSOR_I: J3.4, U1.D38
/SENSOR_J: J3.3, U1.D39
/SENSOR_K: J3.2, U1.D40
/SENSOR_L: J3.1, U1.D41
/TX_EXT: J2.1, U1.D1, U17.DI, U32.4 (DI)
GND: C1.1, C2.1, C3.2, C4.2, C5.1, C6.1, C7.1, C8.1, C9.1, C10.1, C11.1, C12.1, C13.1, C14.1, C15.1, C16.1, D1.1 (VSS), D2.1 (VSS), D3.1 (VSS), D4.1 (VSS), D5.1 (VSS), D6.1 (VSS), D7.1 (VSS), D8.1 (VSS), D9.1 (VSS), D10.1 (VSS), D11.1 (VSS), D12.1 (VSS), J1.2, J2.3, J5.1, J5.2, J5.3, J5.4, J5.5, J5.6, J5.7, J5.8, J5.9, J5.10, J5.11, J5.12, R17.2, R18.2, U1.GND, U2.4 (GND), U3.GND, U3.IN5, U3.IN6, U3.IN7, U4.GND, U4.IN5, U4.IN6, U4.IN7, U5.GND, U5.IN5, U5.IN6, U5.IN7, U6.GND, U6.IN5, U6.IN6, U6.IN7, U7.GND, U7.IN5, U7.IN6, U7.IN7, U8.GND, U8.IN5, U8.IN6, U8.IN7, U9.GND, U9.IN5, U9.IN6, U9.IN7, U10.GND, U10.IN5, U10.IN6, U10.IN7, U11.GND, U12.GND, U12.IN5, U12.IN6, U12.IN7, U13.GND, U13.IN5, U13.IN6, U13.IN7, U14.GND, U14.IN5, U14.IN6, U14.IN7, U15.GND, U15.IN5, U15.IN6, U15.IN7, U17.GND, U31.GND, U32.5 (GND), U33.6 (GND)
unnamed: D1.4 (DOUT), D2.2 (DIN)
unnamed: D2.4 (DOUT), D3.2 (DIN)
unnamed: D3.4 (DOUT), D4.2 (DIN)
unnamed: D4.4 (DOUT), D5.2 (DIN)
unnamed: D5.4 (DOUT), D6.2 (DIN)
unnamed: D6.4 (DOUT), D7.2 (DIN)
unnamed: D7.4 (DOUT), D8.2 (DIN)
unnamed: D8.4 (DOUT), D9.2 (DIN)
unnamed: D9.4 (DOUT), D10.2 (DIN)
unnamed: D10.4 (DOUT), D11.2 (DIN)
unnamed: D11.4 (DOUT), D12.2 (DIN)
unnamed: JP1.1, U1.VIN
unnamed: JP4.2 (B), R17.1, U33.2 (A0)
unnamed: JP5.2 (B), R18.1, U33.1 (A1)

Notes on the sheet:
MCU Option 1: Mega2560 + SSD1306 OLED
Optional: RS485 comms/UART voltage shifting
Motor Driver Modules
Sensor Connectors
Optional: Current sense To omit, install a jumper wire across 12V SENSE. There are 3 options: - "Adafruit-style" wide module (blue) - narrow module (purple) - populate IC and supporting components directly on PCB For modules, install wires from screw terminals on the module to 12V SENSE screw termi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
Connectors
Configuration options: Mega 2560: DNP U16; External RX/TX = 5V; do not use JP2/JP3 ESP32/ESP8266: For 5V RX/TX: Use U16; do not use JP2/JP3 For 3.3V RX/TX: DNP U16; set JP2 and JP3
RS485 Requires 5V RX/TX - for ESP32/ESP8266 must use level shifter
VIN- and VIN+ are not connected via module headers because max current is near the limit of pin headers. Use screw terminals instead.
3A minimum rating, 5A+ preferred
TODO: bypass capacitors
Dedicated SDA/SCL pins are used, so these must be left disconnected.

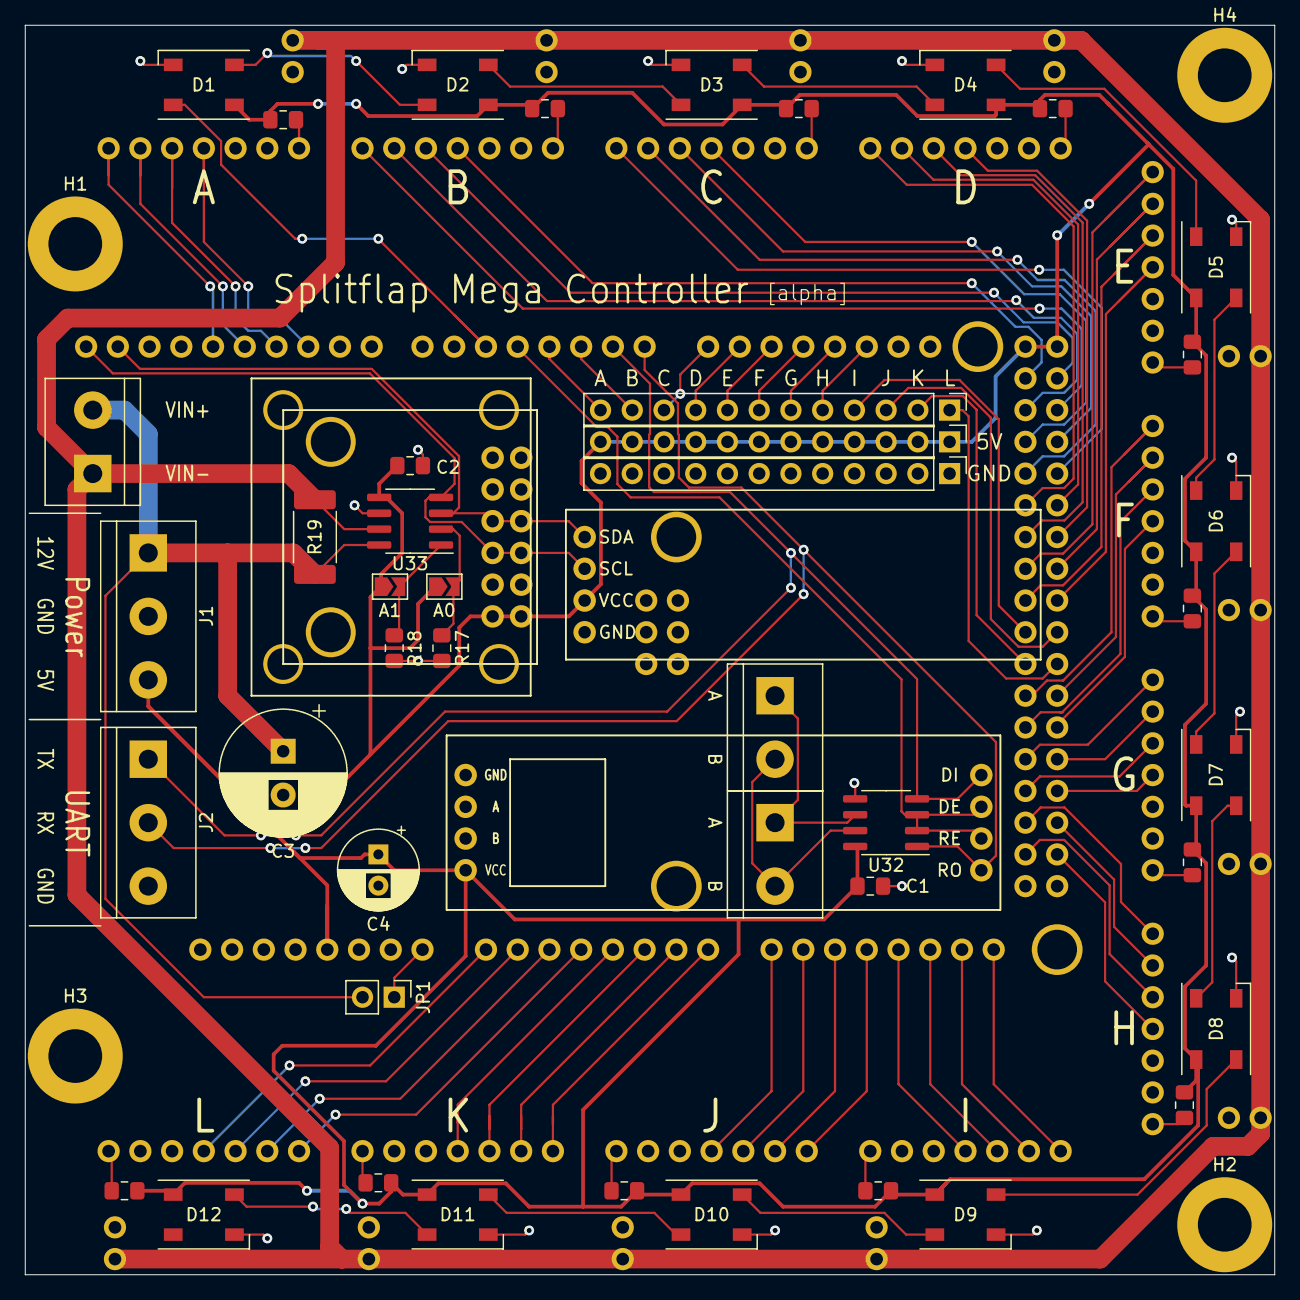
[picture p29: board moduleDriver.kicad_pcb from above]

Board: 2 copper layers, 100.0 x 100.0 mm, 65 parts (0 on the bottom side), 86 nets.

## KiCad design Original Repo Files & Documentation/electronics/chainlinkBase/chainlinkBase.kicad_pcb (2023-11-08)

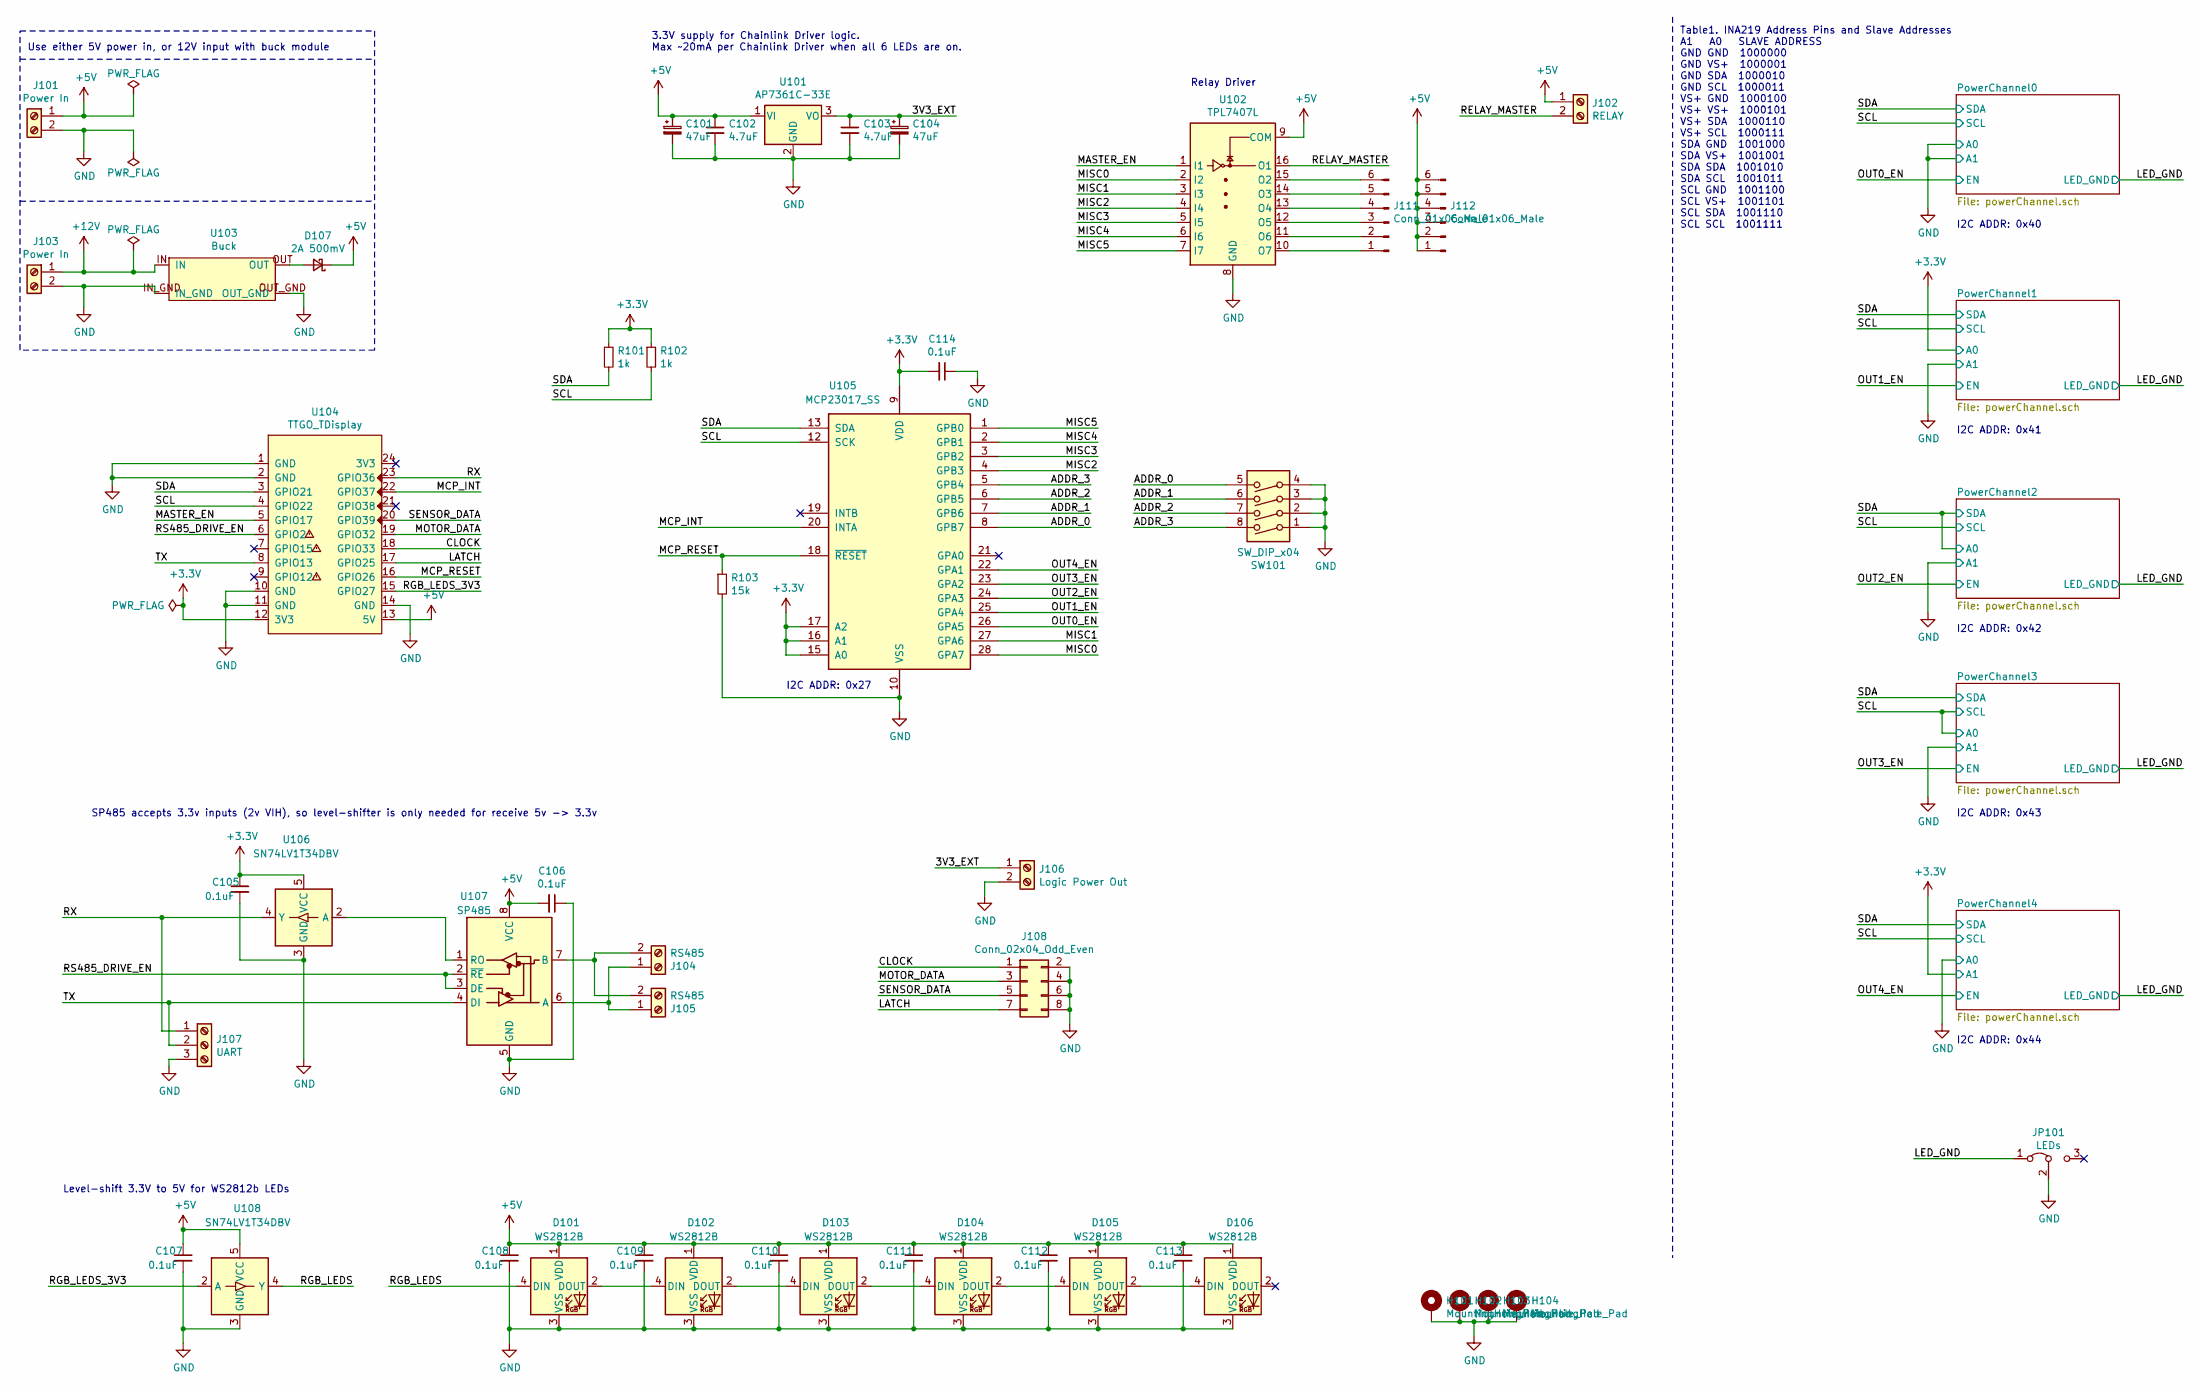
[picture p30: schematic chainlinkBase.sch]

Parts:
C101, C104: 47uF; CP_Elec_6.3x5.4
C102, C103: 4.7uF; C_0805_2012Metric
C105, C106, C107, C108, C109, C110, C111, C112, C113, C114: 0.1uF; C_0805_2012Metric
D101, D102, D103, D104, D105, D106: WS2812B; LED_WS2812B_PLCC4_5.0x5.0mm_P3.2mm
D107: 2A 500mV; D_SOD-128
H101, H102, H103, H104: MountingHole_Pad; MountingHole_3.2mm_M3_ISO7380_Pad
J101, J103: Power In; Generic-5.08-2P
J102: RELAY; Generic-5.08-2P
J104, J105: RS485; Generic-5.08-2P
J106: Logic Power Out; Generic-5.08-2P
J107: UART; Generic-5.08-3P
J108: Conn_02x04_Odd_Even; IDC-Header_2x04_P2.54mm_Vertical
J111, J112: Conn_01x06_Male; PinHeader_1x06_P2.54mm_Vertical
JP101: LEDs; PinHeader_1x03_P2.54mm_Vertical_SolderJumper
R101, R102: 1k; R_0805_2012Metric
R103: 15k; R_0805_2012Metric
SW101: SW_DIP_x04; SW_DIP_SPSTx04_Slide_Omron_A6S-410x_W8.9mm_P2.54mm
U101: AP7361C-33E; SOT-223-3_TabPin2
U102: TPL7407L; SOIC-16_3.9x9.9mm_P1.27mm_silk
U103: Buck; BuckModuleBackSilk
U104: TTGO_TDisplay; T-DISPLAY_extra_pins_labeled
U105: MCP23017_SS; SSOP-28_5.3x10.2mm_P0.65mm
U106, U108: SN74LV1T34DBV; SOT-23-5
U107: SP485; SOIC-8_3.9x4.9mm_P1.27mm

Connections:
+3V3: C105.1, C114.2, R101.1, R102.1, U104.12 (3V3), U105.9 (VDD), U105.15 (A0), U105.16 (A1), U105.17 (A2), U106.5 (VCC); also elsewhere on the board
+5V: C101.1, C102.1, C106.2, C107.1, C108.1, C109.1, C110.1, C111.1, C112.1, C113.1, D101.1 (VDD), D102.1 (VDD), D103.1 (VDD), D104.1 (VDD), D105.1 (VDD), D106.1 (VDD), D107.1 (K), J101.1, J102.1, J112.1, J112.2, J112.3, J112.4, J112.5, J112.6, U101.1 (VI), U102.9 (COM), U104.13 (5V), U107.8 (VCC), U108.5 (VCC)
+12V: J103.1, U103.IN
/3V3_EXT: C103.1, C104.1, J106.1, U101.3 (VO)
/ADDR_0: SW101.5, U105.8 (GPB7)
/ADDR_1: SW101.6, U105.7 (GPB6)
/ADDR_2: SW101.7, U105.6 (GPB5)
/ADDR_3: SW101.8, U105.5 (GPB4)
/CLOCK: J108.1, U104.18 (GPIO33)
/LATCH: J108.7, U104.17 (GPIO25)
/LED_GND: JP101.1 (A); also elsewhere on the board
/MASTER_EN: U102.1 (I1), U104.5 (GPIO17)
/MCP_INT: U104.22 (GPIO37), U105.20 (INTA)
/MCP_RESET: R103.1, U104.16 (GPIO26), U105.18 (~RESET~)
/MISC0: U102.2 (I2), U105.28 (GPA7)
/MISC1: U102.3 (I3), U105.27 (GPA6)
/MISC2: U102.4 (I4), U105.4 (GPB3)
/MISC3: U102.5 (I5), U105.3 (GPB2)
/MISC4: U102.6 (I6), U105.2 (GPB1)
/MISC5: U102.7 (I7), U105.1 (GPB0)
/MOTOR_DATA: J108.3, U104.19 (GPIO32)
/OUT0_EN: U105.26 (GPA5); also elsewhere on the board
/OUT1_EN: U105.25 (GPA4); also elsewhere on the board
/OUT2_EN: U105.24 (GPA3); also elsewhere on the board
/OUT3_EN: U105.23 (GPA2); also elsewhere on the board
/OUT4_EN: U105.22 (GPA1); also elsewhere on the board
/RELAY_MASTER: J102.2, U102.16 (O1)
/RGB_LEDS: D101.4 (DIN), U108.4 (Y)
/RGB_LEDS_3V3: U104.15 (GPIO27), U108.2 (A)
/RS485_DRIVE_EN: U104.6 (GPIO2), U107.2 (~RE), U107.3 (DE)
/RX: J107.1, U104.23 (GPIO36), U106.4 (Y)
/SCL: R102.2, U104.4 (GPIO22), U105.12 (SCK); also elsewhere on the board
/SDA: R101.2, U104.3 (GPIO21), U105.13 (SDA); also elsewhere on the board
/SENSOR_DATA: J108.5, U104.20 (GPIO39)
/TX: J107.2, U104.8 (GPIO13), U107.4 (DI)
GND: C101.2, C102.2, C103.2, C104.2, C105.2, C106.1, C107.2, C108.2, C109.2, C110.2, C111.2, C112.2, C113.2, C114.1, D101.3 (VSS), D102.3 (VSS), D103.3 (VSS), D104.3 (VSS), D105.3 (VSS), D106.3 (VSS), H101.1, H102.1, H103.1, H104.1, J101.2, J103.2, J106.2, J107.3, J108.2, J108.4, J108.6, J108.8, JP101.2 (C), R103.2, SW101.1, SW101.2, SW101.3, SW101.4, U101.2 (GND), U102.8 (GND), U103.IN_GND, U103.OUT_GND, U104.1 (GND), U104.2 (GND), U104.10 (GND), U104.11 (GND), U104.14 (GND), U105.10 (VSS), U106.3 (GND), U107.5 (GND), U108.3 (GND); also elsewhere on the board
unnamed: D101.2 (DOUT), D102.4 (DIN)
unnamed: D102.2 (DOUT), D103.4 (DIN)
unnamed: D103.2 (DOUT), D104.4 (DIN)
unnamed: D104.2 (DOUT), D105.4 (DIN)
unnamed: D105.2 (DOUT), D106.4 (DIN)
unnamed: D107.2 (A), U103.OUT
unnamed: J104.1, J105.1, U107.6 (A)
unnamed: J104.2, J105.2, U107.7 (B)
unnamed: J111.1, U102.10 (O7)
unnamed: J111.2, U102.11 (O6)
unnamed: J111.3, U102.12 (O5)
unnamed: J111.4, U102.13 (O4)
unnamed: J111.5, U102.14 (O3)
unnamed: J111.6, U102.15 (O2)
unnamed: U106.2 (A), U107.1 (RO)

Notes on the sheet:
Relay Driver
I2C ADDR: 0x27
I2C ADDR: 0x40
Level-shift 3.3V to 5V for WS2812b LEDs
SP485 accepts 3.3v inputs (2v VIH), so level-shifter is only needed for receive 5v -> 3.3v
3.3V supply for Chainlink Driver logic. Max ~~20mA per Chainlink Driver when all 6 LEDs are on.
Use either 5V power in, or 12V input with buck module
Table1. INA219 Address Pins and Slave Addresses A1 A0 SLAVE ADDRESS GND GND 1000000 GND VS+ 1000001 GND SDA 1000010 GND SCL 1000011 VS+ GND 1000100 VS+ VS+ 1000101 VS+ SDA 1000110 VS+ SCL 1000111 SDA GND 1001000 SDA VS+ 1001001 SDA SDA 1001010 SDA SCL 1001011 SCL GND 1001100 SCL VS+ 1001101 SCL SDA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
I2C ADDR: 0x41
I2C ADDR: 0x42
I2C ADDR: 0x43
I2C ADDR: 0x44

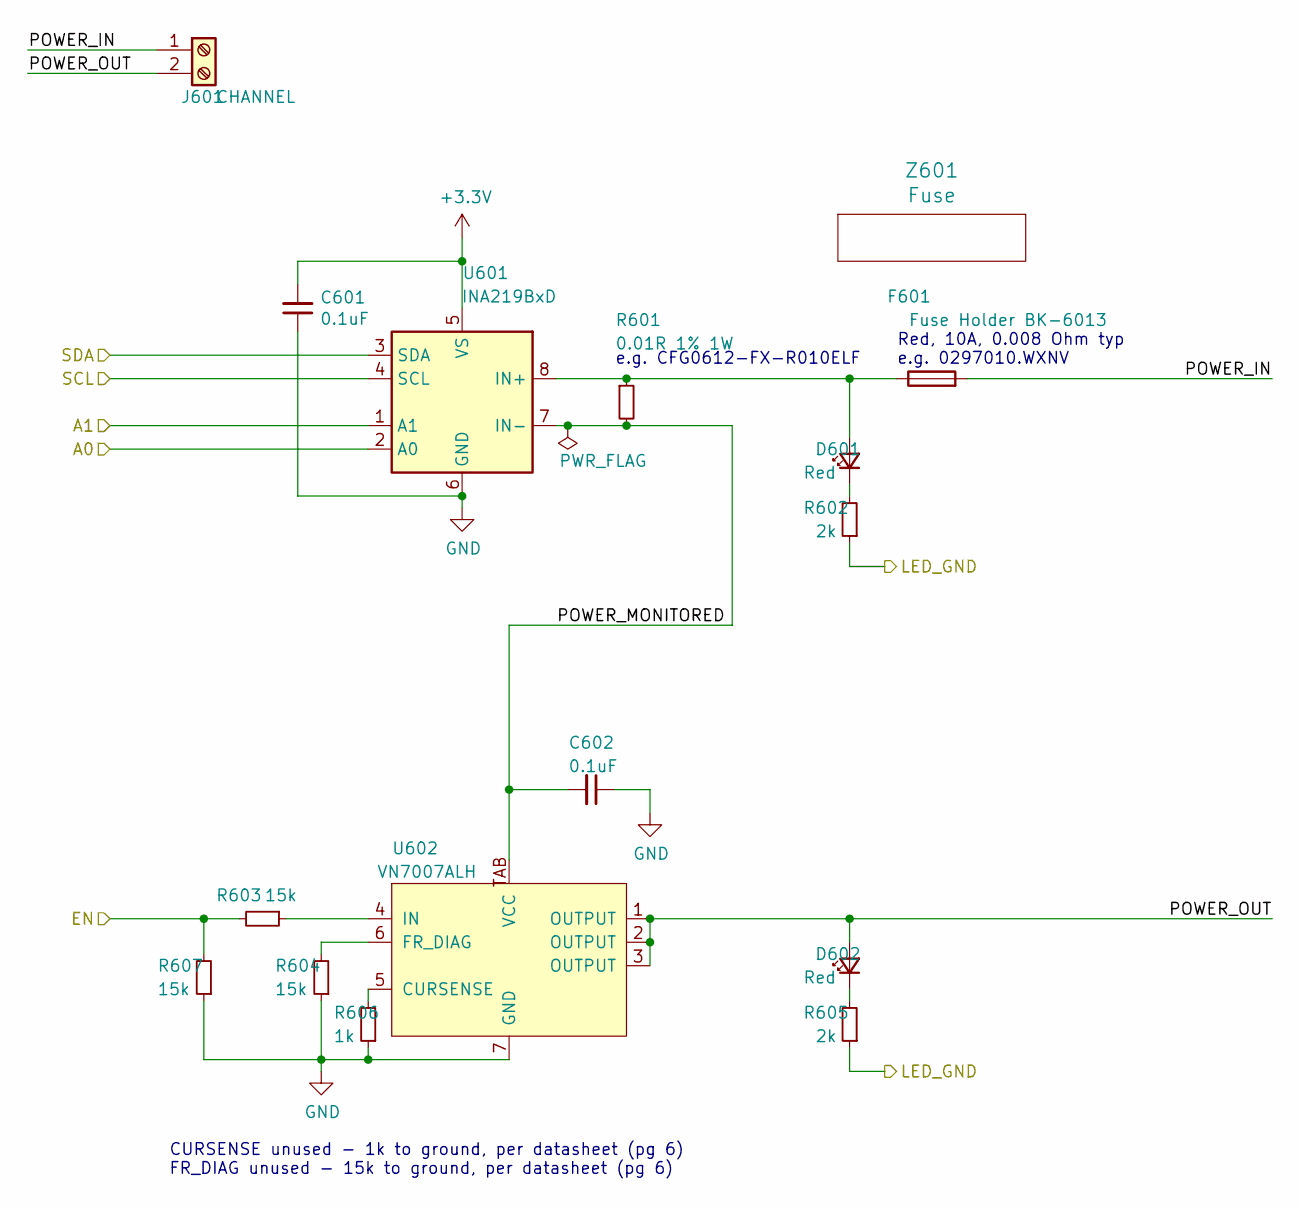
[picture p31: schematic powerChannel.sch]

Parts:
C201, C202: 0.1uF; C_0805_2012Metric
D201, D202: Red; LED_0805_2012Metric_Silkscreen
F201: Fuse Holder BK-6013; BK-6013
J201: CHANNEL; Generic-5.08-2P
R201: 0.01R 1% 1W; R_0612_1632Metric
R202, R205: 2k; R_0805_2012Metric
R203, R204, R207: 15k; R_0805_2012Metric
R206: 1k; R_0805_2012Metric
U201: INA219BxD; SOIC-8_3.9x4.9mm_P1.27mm
U202: VN7007ALH; VN7007ALHTR
Z201: Fuse; Dummy

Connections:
+3V3: C201.2, U201.5 (VS); also elsewhere on the board
/LED_GND: R202.1, R205.1; also elsewhere on the board
/OUT0_EN: R203.2, R207.2; also elsewhere on the board
/PowerChannel0/POWER_IN: F201.2, J201.1
/PowerChannel0/POWER_MONITORED: C202.2, R201.2, U201.7 (IN-), U202.TAB (VCC)
/PowerChannel0/POWER_OUT: D202.2 (A), J201.2, U202.1 (OUTPUT), U202.2 (OUTPUT), U202.3 (OUTPUT)
/SCL: U201.4 (SCL); also elsewhere on the board
/SDA: U201.3 (SDA); also elsewhere on the board
GND: C201.1, C202.1, R204.1, R206.1, R207.1, U201.1 (A1), U201.2 (A0), U201.6 (GND), U202.7 (GND); also elsewhere on the board
unnamed: D201.1 (K), R202.2
unnamed: D201.2 (A), F201.1, R201.1, U201.8 (IN+)
unnamed: D202.1 (K), R205.2
unnamed: R203.1, U202.4 (IN)
unnamed: R204.2, U202.6 (FR_DIAG)
unnamed: R206.2, U202.5 (CURSENSE)

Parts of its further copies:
C301, C302, C401, C402, C501, C502, C601, C602: 0.1uF; C_0805_2012Metric
D301, D302, D401, D402, D501, D502, D601, D602: Red; LED_0805_2012Metric_Silkscreen
F301, F401, F501, F601: Fuse Holder BK-6013; BK-6013
J301, J401, J501, J601: CHANNEL; Generic-5.08-2P
R301, R401, R501, R601: 0.01R 1% 1W; R_0612_1632Metric
R302, R305, R402, R405, R502, R505, R602, R605: 2k; R_0805_2012Metric
R303, R304, R307, R403, R404, R407, R503, R504, R507, R603, R604, R607: 15k; R_0805_2012Metric
R306, R406, R506, R606: 1k; R_0805_2012Metric
U301, U401, U501, U601: INA219BxD; SOIC-8_3.9x4.9mm_P1.27mm
U302, U402, U502, U602: VN7007ALH; VN7007ALHTR
Z301, Z401, Z501, Z601: Fuse; Dummy

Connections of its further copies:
+3V3: C301.2, C401.2, C501.2, C601.2, U301.2 (A0), U301.5 (VS), U401.5 (VS), U501.5 (VS), U601.1 (A1), U601.5 (VS); also elsewhere on the board
/LED_GND: R302.1, R305.1, R402.1, R405.1, R502.1, R505.1, R602.1, R605.1; also elsewhere on the board
/OUT1_EN: R303.2, R307.2; also elsewhere on the board
/OUT2_EN: R403.2, R407.2; also elsewhere on the board
/OUT3_EN: R503.2, R507.2; also elsewhere on the board
/OUT4_EN: R603.2, R607.2; also elsewhere on the board
/PowerChannel1/POWER_IN: F301.2, J301.1
/PowerChannel1/POWER_MONITORED: C302.2, R301.2, U301.7 (IN-), U302.TAB (VCC)
/PowerChannel1/POWER_OUT: D302.2 (A), J301.2, U302.1 (OUTPUT), U302.2 (OUTPUT), U302.3 (OUTPUT)
/PowerChannel2/POWER_IN: F401.2, J401.1
/PowerChannel2/POWER_MONITORED: C402.2, R401.2, U401.7 (IN-), U402.TAB (VCC)
/PowerChannel2/POWER_OUT: D402.2 (A), J401.2, U402.1 (OUTPUT), U402.2 (OUTPUT), U402.3 (OUTPUT)
/PowerChannel3/POWER_IN: F501.2, J501.1
/PowerChannel3/POWER_MONITORED: C502.2, R501.2, U501.7 (IN-), U502.TAB (VCC)
/PowerChannel3/POWER_OUT: D502.2 (A), J501.2, U502.1 (OUTPUT), U502.2 (OUTPUT), U502.3 (OUTPUT)
/PowerChannel4/POWER_IN: F601.2, J601.1
/PowerChannel4/POWER_MONITORED: C602.2, R601.2, U601.7 (IN-), U602.TAB (VCC)
/PowerChannel4/POWER_OUT: D602.2 (A), J601.2, U602.1 (OUTPUT), U602.2 (OUTPUT), U602.3 (OUTPUT)
/SCL: U301.4 (SCL), U401.4 (SCL), U501.2 (A0), U501.4 (SCL), U601.4 (SCL); also elsewhere on the board
/SDA: U301.3 (SDA), U401.2 (A0), U401.3 (SDA), U501.3 (SDA), U601.3 (SDA); also elsewhere on the board
GND: C301.1, C302.1, C401.1, C402.1, C501.1, C502.1, C601.1, C602.1, R304.1, R306.1, R307.1, R404.1, R406.1, R407.1, R504.1, R506.1, R507.1, R604.1, R606.1, R607.1, U301.1 (A1), U301.6 (GND), U302.7 (GND), U401.1 (A1), U401.6 (GND), U402.7 (GND), U501.1 (A1), U501.6 (GND), U502.7 (GND), U601.2 (A0), U601.6 (GND), U602.7 (GND); also elsewhere on the board
unnamed: D301.1 (K), R302.2
unnamed: D301.2 (A), F301.1, R301.1, U301.8 (IN+)
unnamed: D302.1 (K), R305.2
unnamed: D401.1 (K), R402.2
unnamed: D401.2 (A), F401.1, R401.1, U401.8 (IN+)
unnamed: D402.1 (K), R405.2
unnamed: D501.1 (K), R502.2
unnamed: D501.2 (A), F501.1, R501.1, U501.8 (IN+)
unnamed: D502.1 (K), R505.2
unnamed: D601.1 (K), R602.2
unnamed: D601.2 (A), F601.1, R601.1, U601.8 (IN+)
unnamed: D602.1 (K), R605.2
unnamed: R303.1, U302.4 (IN)
unnamed: R304.2, U302.6 (FR_DIAG)
unnamed: R306.2, U302.5 (CURSENSE)
unnamed: R403.1, U402.4 (IN)
unnamed: R404.2, U402.6 (FR_DIAG)
unnamed: R406.2, U402.5 (CURSENSE)
unnamed: R503.1, U502.4 (IN)
unnamed: R504.2, U502.6 (FR_DIAG)
unnamed: R506.2, U502.5 (CURSENSE)
unnamed: R603.1, U602.4 (IN)
unnamed: R604.2, U602.6 (FR_DIAG)
unnamed: R606.2, U602.5 (CURSENSE)

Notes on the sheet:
e.g. CFG0612-FX-R010ELF
Red, 10A, 0.008 Ohm typ e.g. 0297010.WXNV
CURSENSE unused - 1k to ground, per datasheet (pg 6) FR_DIAG unused - 15k to ground, per datasheet (pg 6)

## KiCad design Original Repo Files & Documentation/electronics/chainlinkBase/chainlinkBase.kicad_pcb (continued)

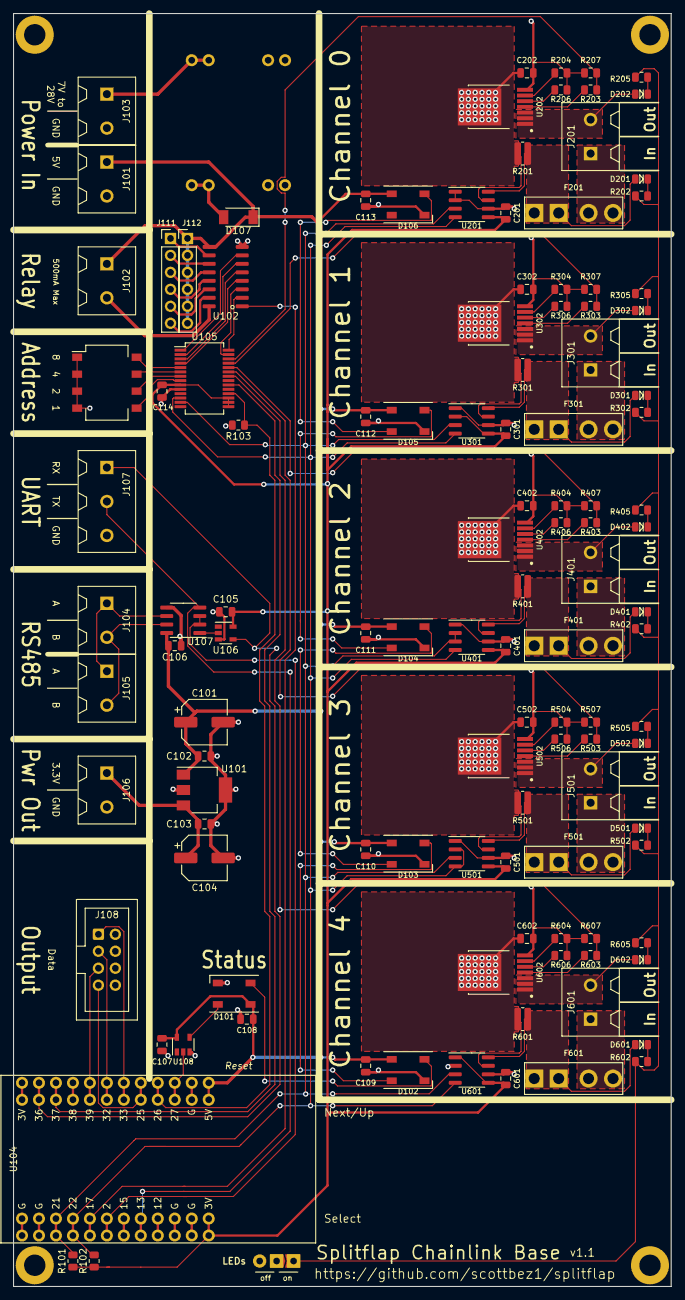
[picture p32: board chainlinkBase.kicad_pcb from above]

Board: 2 copper layers, 98.4 x 190.5 mm, 128 parts (0 on the bottom side), 96 nets.

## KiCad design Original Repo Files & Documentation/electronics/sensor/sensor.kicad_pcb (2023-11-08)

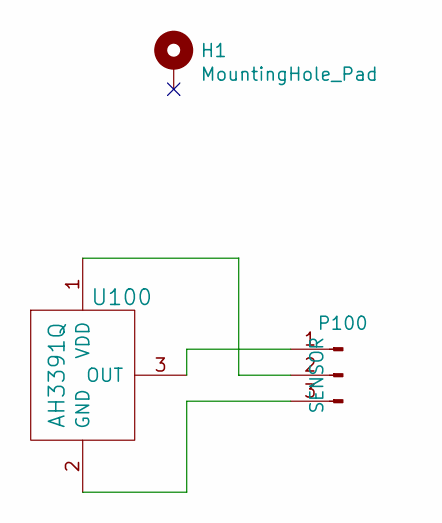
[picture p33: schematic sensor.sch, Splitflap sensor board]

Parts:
H1: MountingHole_Pad; M4_mount
P100: SENSOR; Pin_Header_Right_Angle_1x03
U100: AH3391Q; hall_effect_wide

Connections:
unnamed: P100.1, U100.3 (OUT)
unnamed: P100.2, U100.1 (VDD)
unnamed: P100.3, U100.2 (GND)

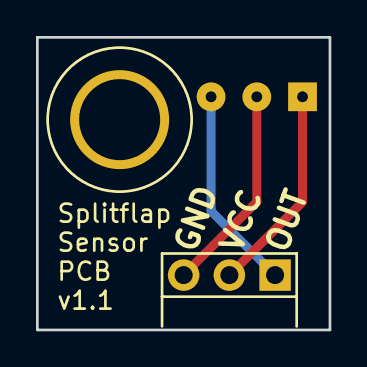
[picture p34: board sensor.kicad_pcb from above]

Board: 2 copper layers, 16.3 x 16.3 mm, 3 parts (1 on the bottom side), 3 nets.

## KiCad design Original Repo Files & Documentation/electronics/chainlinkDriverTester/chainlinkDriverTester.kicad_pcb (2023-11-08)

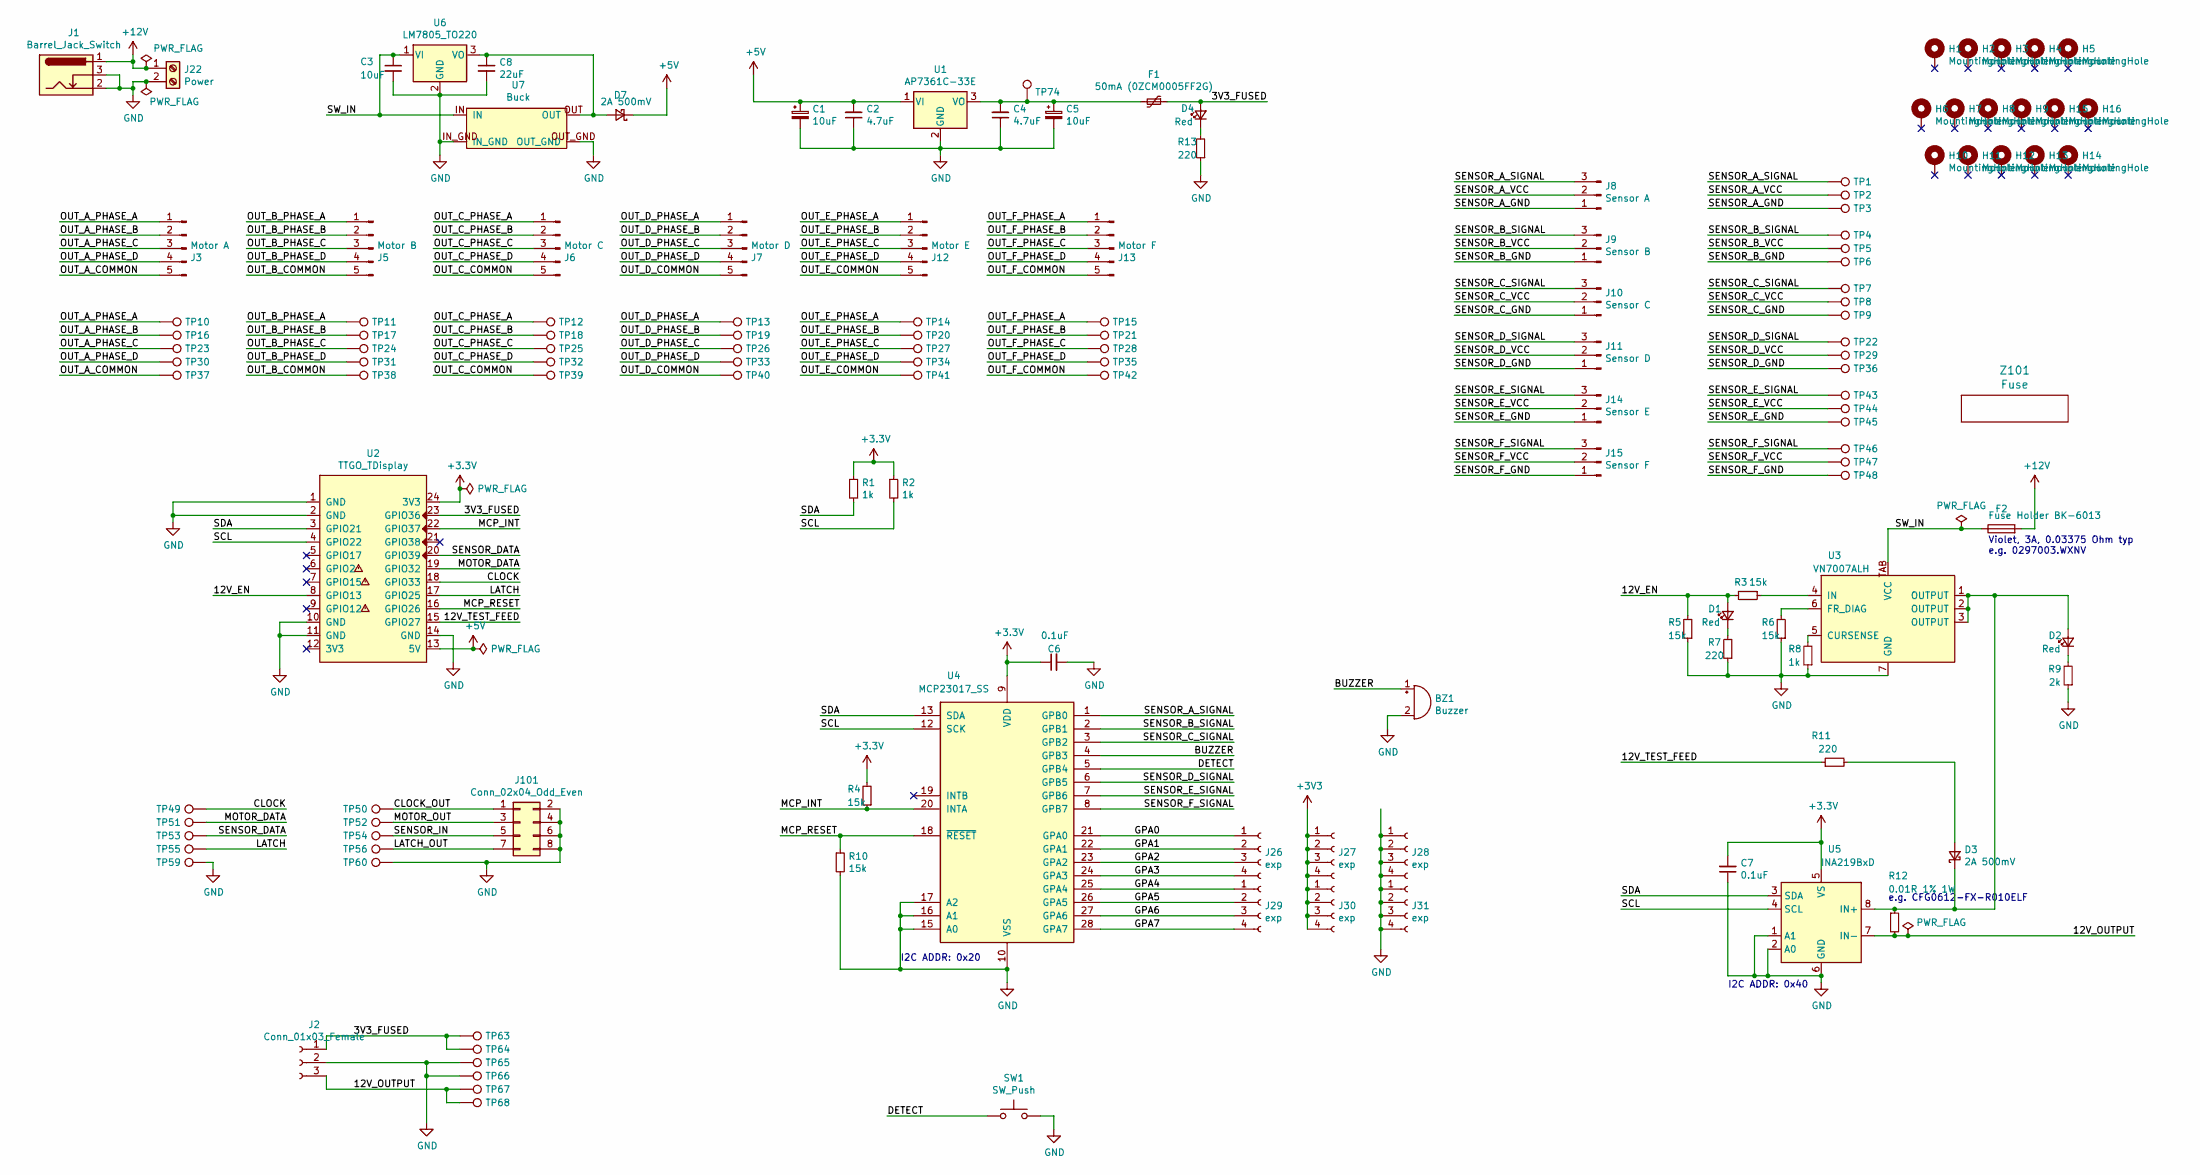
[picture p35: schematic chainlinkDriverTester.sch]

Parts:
BZ1: Buzzer; Buzzer_12x9.5RM7.6
C1, C5: 10uF; CP_Elec_4x5.3; LCSC C134721
C2, C4: 4.7uF; C_0805_2012Metric
C3: 10uF; C_1206_3216Metric
C6, C7: 0.1uF; C_0805_2012Metric
C8: 22uF; C_1206_3216Metric
D1, D2, D4: Red; LED_0805_2012Metric_Silkscreen
D3, D7: 2A 500mV; D_SOD-128
F1: 50mA (0ZCM0005FF2G); Fuse_0603_1608Metric
F2: Fuse Holder BK-6013; BK-6013
H1, H2, H3, H4, H5, H6, H7, H8, H9, H10, H11, H12, H13, H14, H15, H16: MountingHole; MountingHole_3.2mm_M3_ISO7380_Pad
J1: Barrel_Jack_Switch; PJ-202A
J2: Conn_01x03_Female; PinSocket_1x03_P2.54mm_Vertical
J3: Motor A; JST_XH_B5B-XH-A_1x05_P2.50mm_Vertical
J5: Motor B; JST_XH_B5B-XH-A_1x05_P2.50mm_Vertical
J6: Motor C; JST_XH_B5B-XH-A_1x05_P2.50mm_Vertical
J7: Motor D; JST_XH_B5B-XH-A_1x05_P2.50mm_Vertical
J8: Sensor A; PinHeader_1x03_P2.54mm_Vertical
J9: Sensor B; PinHeader_1x03_P2.54mm_Vertical
J10: Sensor C; PinHeader_1x03_P2.54mm_Vertical
J11: Sensor D; PinHeader_1x03_P2.54mm_Vertical
J12: Motor E; JST_XH_B5B-XH-A_1x05_P2.50mm_Vertical
J13: Motor F; JST_XH_B5B-XH-A_1x05_P2.50mm_Vertical
J14: Sensor E; PinHeader_1x03_P2.54mm_Vertical
J15: Sensor F; PinHeader_1x03_P2.54mm_Vertical
J22: Power; Generic-5.08-2P; LCSC C8465
J26, J27, J28, J29, J30, J31: exp; PinHeader_1x04_P2.54mm_Vertical
J101: Conn_02x04_Odd_Even; IDC-Header_2x04_P2.54mm_Vertical
R1, R2, R8: 1k; R_0805_2012Metric
R3, R4, R5, R6, R10: 15k; R_0805_2012Metric
R7, R11, R13: 220; R_0805_2012Metric
R9: 2k; R_0805_2012Metric
R12: 0.01R 1% 1W; R_0612_1632Metric
SW1: SW_Push; ESE13V01D
TP1, TP2, TP3, TP4, TP5, TP6, TP7, TP8, TP9, TP10, TP11, TP12, TP13, TP14, TP15, TP16, TP17, TP18, TP19, TP20, TP21, TP22, TP23, TP24, TP25, TP26, TP27, TP28, TP29, TP30, TP31, TP32, TP33, TP34, TP35, TP36, TP37, TP38, TP39, TP40, TP41, TP42, TP43, TP44, TP45, TP46, TP47, TP48, TP49, TP50, TP51, TP52, TP53, TP54, TP55, TP56, TP59, TP60, TP63, TP64, TP65, TP66, TP67, TP68: TestPoint; pogo1mm
TP74: TestPoint; TestPoint_THTPad_D2.0mm_Drill1.0mm
U1: AP7361C-33E; SOT-223-3_TabPin2
U2: TTGO_TDisplay; T-DISPLAY_extra_pins
U3: VN7007ALH; VN7007ALHTR
U4: MCP23017_SS; SSOP-28_5.3x10.2mm_P0.65mm
U5: INA219BxD; SOIC-8_3.9x4.9mm_P1.27mm
U6: LM7805_TO220; TO-220-3_Vertical
U7: Buck; BuckModuleBackSilk
Z101: Fuse; Dummy

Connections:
+5V: C1.1, C2.2, D7.1 (K), U1.1 (VI), U2.13 (5V)
+12V: F2.2, J1.1, J22.1
/3V3_FUSED: D4.2 (A), F1.1, J2.1, TP63.1, TP64.1, U2.23 (GPIO36)
/12V_EN: D1.2 (A), R3.2, R5.2, U2.8 (GPIO13)
/12V_OUTPUT: J2.3, R12.2, TP67.1, TP68.1, U5.7 (IN-)
/12V_TEST_FEED: R11.1, U2.15 (GPIO27)
/BUZZER: BZ1.1 (-), U4.4 (GPB3)
/CLOCK: TP49.1, U2.18 (GPIO33)
/CLOCK_OUT: J101.1, TP50.1
/DETECT: SW1.1, U4.5 (GPB4)
/GPA0: J26.1, U4.21 (GPA0)
/GPA1: J26.2, U4.22 (GPA1)
/GPA2: J26.3, U4.23 (GPA2)
/GPA3: J26.4, U4.24 (GPA3)
/GPA4: J29.1, U4.25 (GPA4)
/GPA5: J29.2, U4.26 (GPA5)
/GPA6: J29.3, U4.27 (GPA6)
/GPA7: J29.4, U4.28 (GPA7)
/LATCH: TP55.1, U2.17 (GPIO25)
/LATCH_OUT: J101.7, TP56.1
/MCP_INT: R4.1, U2.22 (GPIO37), U4.20 (INTA)
/MCP_RESET: R10.1, U2.16 (GPIO26), U4.18 (~RESET~)
/MOTOR_DATA: TP51.1, U2.19 (GPIO32)
/MOTOR_OUT: J101.3, TP52.1
/OUT_A_COMMON: J3.5, TP37.1
/OUT_A_PHASE_A: J3.1, TP10.1
/OUT_A_PHASE_B: J3.2, TP16.1
/OUT_A_PHASE_C: J3.3, TP23.1
/OUT_A_PHASE_D: J3.4, TP30.1
/OUT_B_COMMON: J5.5, TP38.1
/OUT_B_PHASE_A: J5.1, TP11.1
/OUT_B_PHASE_B: J5.2, TP17.1
/OUT_B_PHASE_C: J5.3, TP24.1
/OUT_B_PHASE_D: J5.4, TP31.1
/OUT_C_COMMON: J6.5, TP39.1
/OUT_C_PHASE_A: J6.1, TP12.1
/OUT_C_PHASE_B: J6.2, TP18.1
/OUT_C_PHASE_C: J6.3, TP25.1
/OUT_C_PHASE_D: J6.4, TP32.1
/OUT_D_COMMON: J7.5, TP40.1
/OUT_D_PHASE_A: J7.1, TP13.1
/OUT_D_PHASE_B: J7.2, TP19.1
/OUT_D_PHASE_C: J7.3, TP26.1
/OUT_D_PHASE_D: J7.4, TP33.1
/OUT_E_COMMON: J12.5, TP41.1
/OUT_E_PHASE_A: J12.1, TP14.1
/OUT_E_PHASE_B: J12.2, TP20.1
/OUT_E_PHASE_C: J12.3, TP27.1
/OUT_E_PHASE_D: J12.4, TP34.1
/OUT_F_COMMON: J13.5, TP42.1
/OUT_F_PHASE_A: J13.1, TP15.1
/OUT_F_PHASE_B: J13.2, TP21.1
/OUT_F_PHASE_C: J13.3, TP28.1
/OUT_F_PHASE_D: J13.4, TP35.1
/SCL: R2.2, U2.4 (GPIO22), U4.12 (SCK), U5.4 (SCL)
/SDA: R1.2, U2.3 (GPIO21), U4.13 (SDA), U5.3 (SDA)
/SENSOR_A_GND: J8.1, TP3.1
/SENSOR_A_SIGNAL: J8.3, TP1.1, U4.1 (GPB0)
/SENSOR_A_VCC: J8.2, TP2.1
/SENSOR_B_GND: J9.1, TP6.1
/SENSOR_B_SIGNAL: J9.3, TP4.1, U4.2 (GPB1)
/SENSOR_B_VCC: J9.2, TP5.1
/SENSOR_C_GND: J10.1, TP9.1
/SENSOR_C_SIGNAL: J10.3, TP7.1, U4.3 (GPB2)
/SENSOR_C_VCC: J10.2, TP8.1
/SENSOR_DATA: TP53.1, U2.20 (GPIO39)
/SENSOR_D_GND: J11.1, TP36.1
/SENSOR_D_SIGNAL: J11.3, TP22.1, U4.6 (GPB5)
/SENSOR_D_VCC: J11.2, TP29.1
/SENSOR_E_GND: J14.1, TP45.1
/SENSOR_E_SIGNAL: J14.3, TP43.1, U4.7 (GPB6)
/SENSOR_E_VCC: J14.2, TP44.1
/SENSOR_F_GND: J15.1, TP48.1
/SENSOR_F_SIGNAL: J15.3, TP46.1, U4.8 (GPB7)
/SENSOR_F_VCC: J15.2, TP47.1
/SENSOR_IN: J101.5, TP54.1
/SW_IN: C3.1, F2.1, U3.TAB (VCC), U6.1 (VI), U7.IN
GND: BZ1.2 (+), C1.2, C2.1, C3.2, C4.1, C5.2, C6.2, C7.1, C8.2, J1.2, J1.3, J2.2, J22.2, J28.1, J28.2, J28.3, J28.4, J31.1, J31.2, J31.3, J31.4, J101.2, J101.4, J101.6, J101.8, R5.1, R6.1, R7.1, R8.1, R9.1, R10.2, R13.1, SW1.2, TP59.1, TP60.1, TP65.1, TP66.1, U1.2 (GND), U2.1 (GND), U2.2 (GND), U2.10 (GND), U2.11 (GND), U2.14 (GND), U3.7 (GND), U4.10 (VSS), U4.15 (A0), U4.16 (A1), U4.17 (A2), U5.1 (A1), U5.2 (A0), U5.6 (GND), U6.2 (GND), U7.IN_GND, U7.OUT_GND
unnamed: C4.2, C5.1, F1.2, TP74.1, U1.3 (VO)
unnamed: C8.1, D7.2 (A), U6.3 (VO), U7.OUT
unnamed: D1.1 (K), R7.2
unnamed: D2.1 (K), R9.2
unnamed: D2.2 (A), D3.1 (K), R12.1, U3.1 (OUTPUT), U3.2 (OUTPUT), U3.3 (OUTPUT), U5.8 (IN+)
unnamed: D3.2 (A), R11.2
unnamed: D4.1 (K), R13.2
unnamed: R3.1, U3.4 (IN)
unnamed: R6.2, U3.6 (FR_DIAG)
unnamed: R8.2, U3.5 (CURSENSE)

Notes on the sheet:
Violet, 3A, 0.03375 Ohm typ e.g. 0297003.WXNV
I2C ADDR: 0x40
e.g. CFG0612-FX-R010ELF
I2C ADDR: 0x20

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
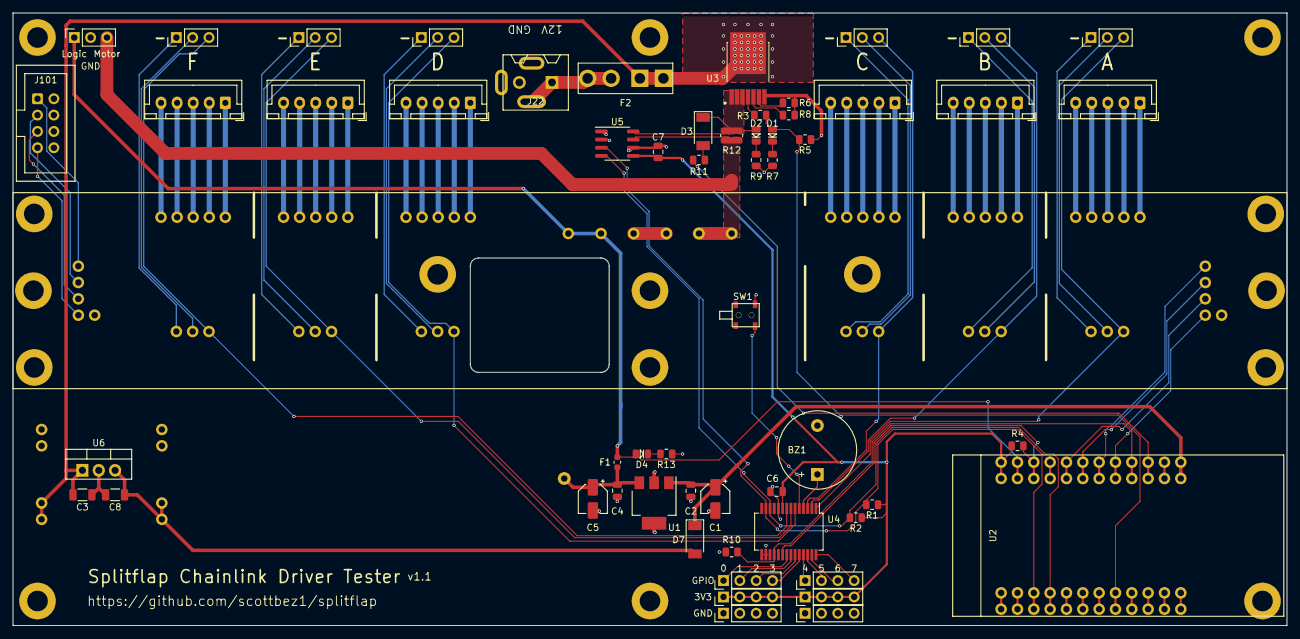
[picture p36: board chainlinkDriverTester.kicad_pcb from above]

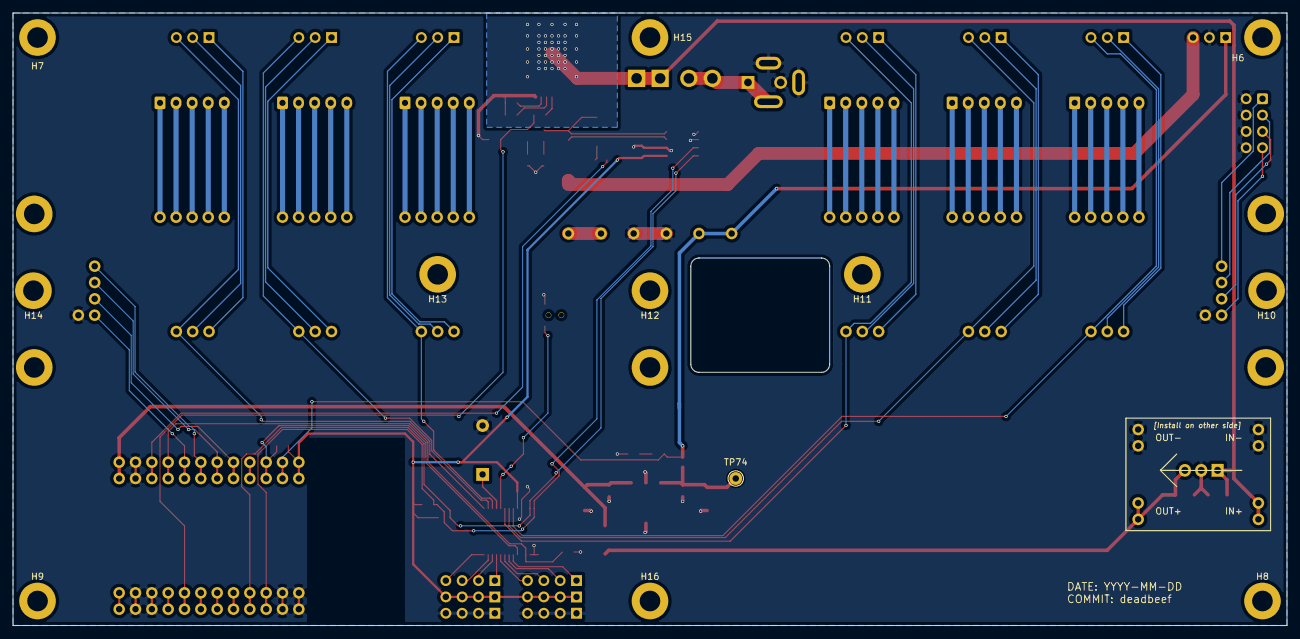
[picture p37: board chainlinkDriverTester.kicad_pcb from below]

Board: 2 copper layers, 198.1 x 95.2 mm, 141 parts (12 on the bottom side), 89 nets.

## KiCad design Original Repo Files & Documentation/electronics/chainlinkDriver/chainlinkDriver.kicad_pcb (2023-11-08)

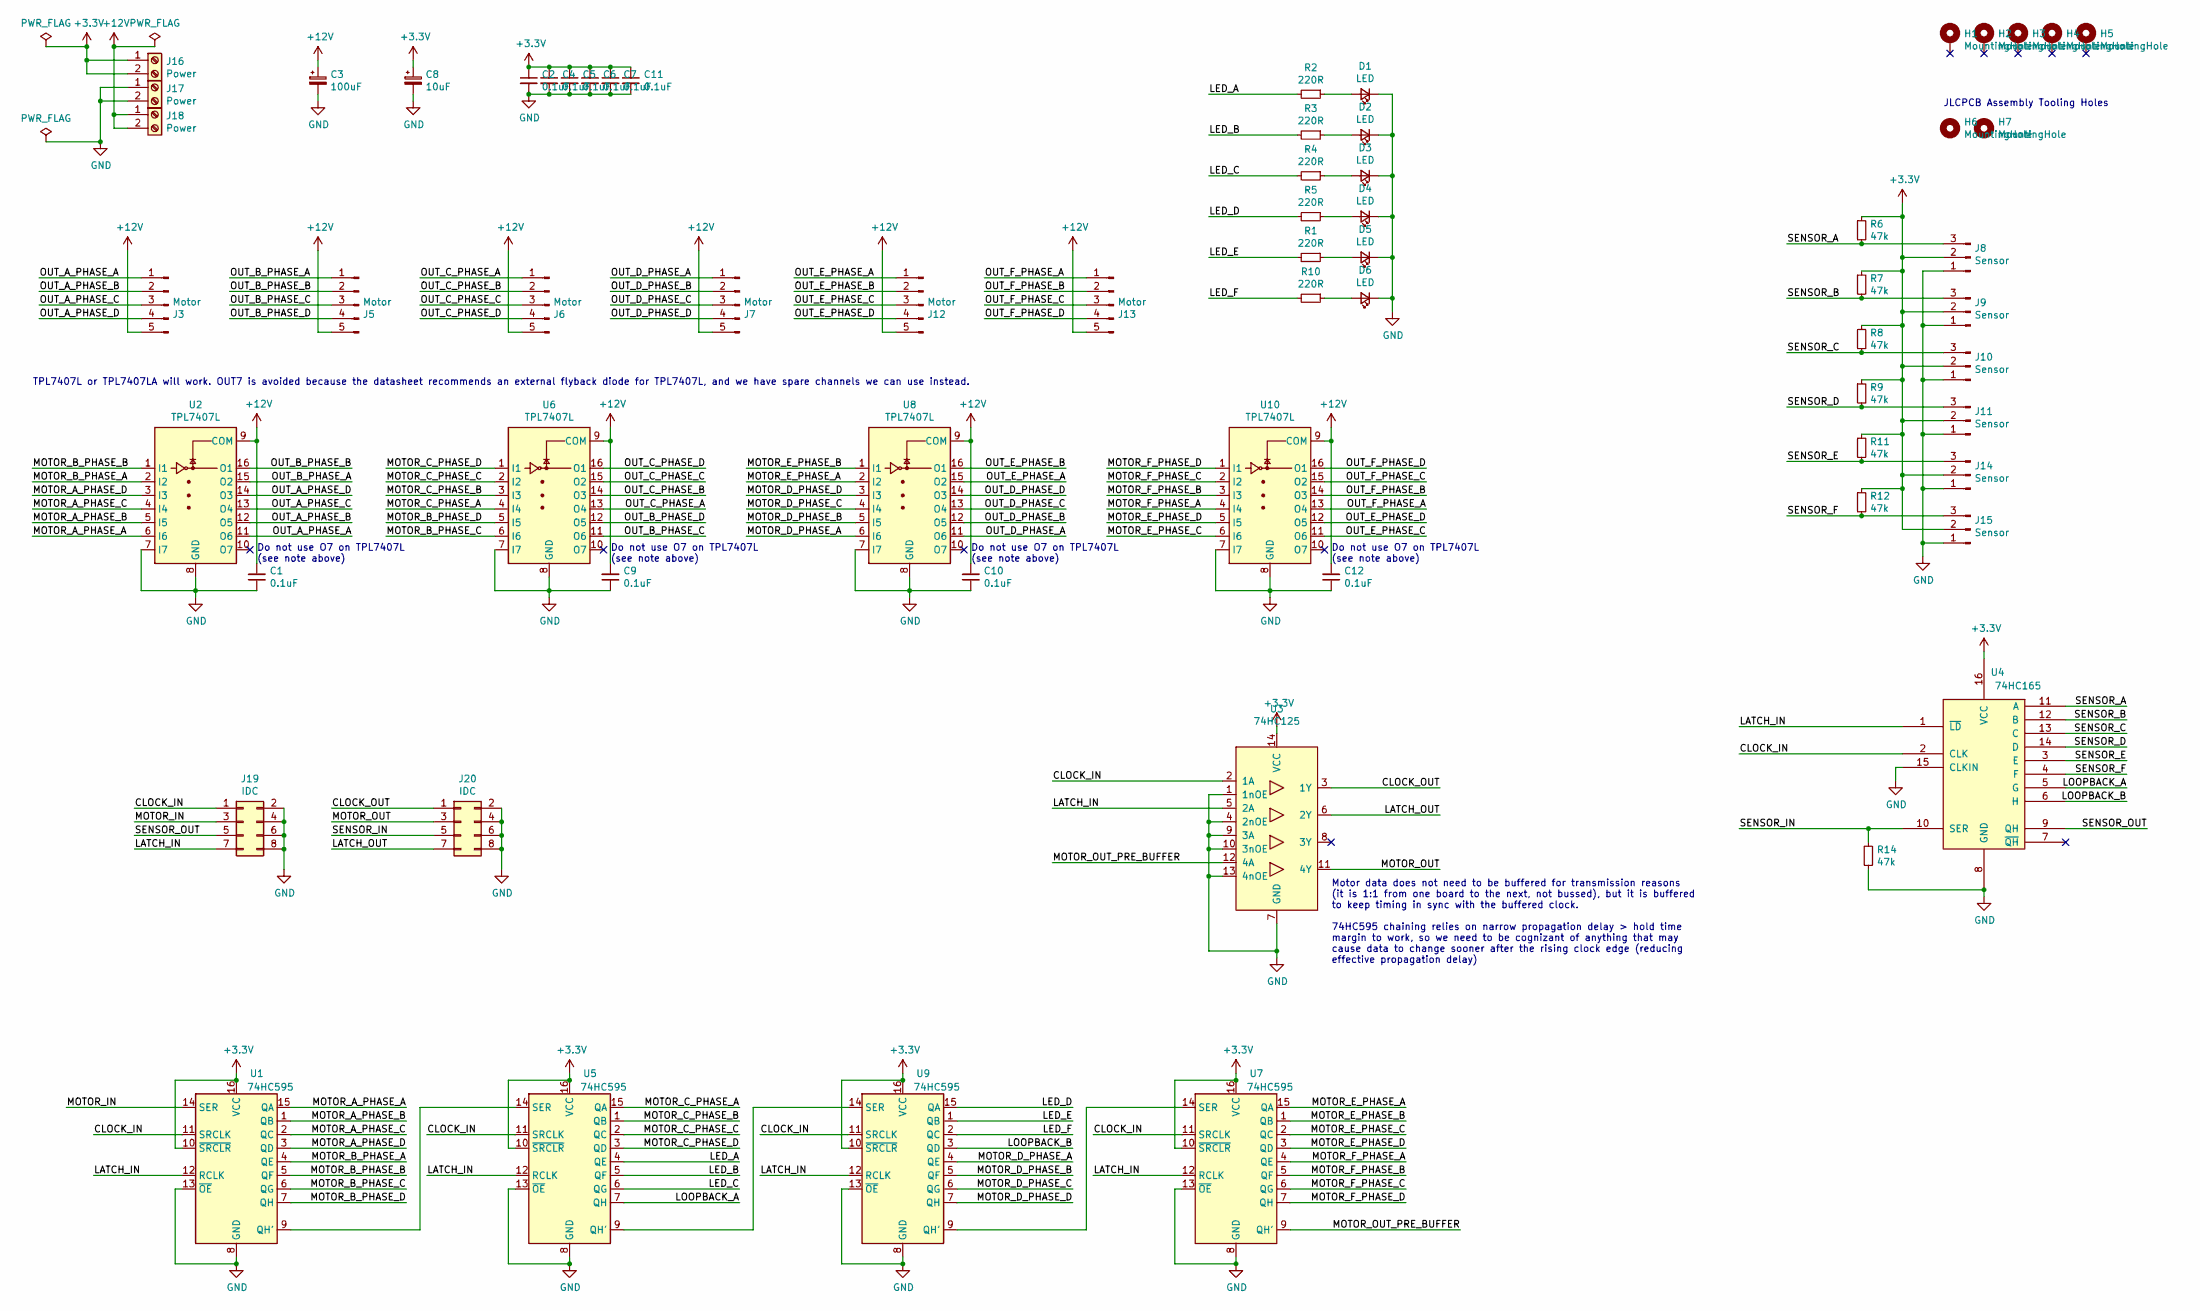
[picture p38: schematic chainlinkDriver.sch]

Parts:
C1, C2, C4, C5, C6, C7, C9, C10, C11, C12: 0.1uF; C_0603_1608Metric; LCSC C14663
C3: 100uF; CP_Elec_8x10; LCSC C176665
C8: 10uF; CP_Elec_4x5.3; LCSC C134721
D1, D2, D3, D4, D5, D6: LED; LED_0603_1608Metric_Silkscreen; LCSC C2286
H1, H2, H3, H4, H5: MountingHole; MountingHole_3.2mm_M3_ISO7380_Pad
H6, H7: MountingHole; AssemblyToolingHole
J3, J5, J6, J7, J12, J13: Motor; JST_XH_B5B-XH-A_1x05_P2.50mm_Vertical
J8, J9, J10, J11, J14, J15: Sensor; PinHeader_1x03_P2.54mm_Vertical
J16, J17, J18: Power; Generic-5.08-2P; LCSC C8465
J19, J20: IDC; IDC-Header_2x04_P2.54mm_Vertical
R1, R2, R3, R4, R5, R10: 220R; R_0603_1608Metric; LCSC C22962
R6, R7, R8, R9, R11, R12, R14: 47k; R_0603_1608Metric; LCSC C25819
U1, U5, U7, U9: 74HC595; SOIC-16_3.9x9.9mm_P1.27mm_silk; LCSC C5947
U2, U6, U8, U10: TPL7407L; SOIC-16_3.9x9.9mm_P1.27mm_silk; LCSC C139663
U3: 74HC125; SOIC-14_3.9x8.7mm_P1.27mm_silk; LCSC C5598
U4: 74HC165; SOIC-16_3.9x9.9mm_P1.27mm_silk; LCSC C5613

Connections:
+3V3: C2.1, C4.1, C5.1, C6.1, C7.1, C8.1, C11.1, J8.2, J9.2, J10.2, J11.2, J14.2, J15.2, J16.1, J16.2, R6.1, R7.1, R8.1, R9.1, R11.1, R12.1, U1.10 (~SRCLR), U1.16 (VCC), U3.14 (VCC), U4.16 (VCC), U5.10 (~SRCLR), U5.16 (VCC), U7.10 (~SRCLR), U7.16 (VCC), U9.10 (~SRCLR), U9.16 (VCC)
+12V: C1.2, C3.1, C9.2, C10.2, C12.2, J3.5, J5.5, J6.5, J7.5, J12.5, J13.5, J18.1, J18.2, U2.9 (COM), U6.9 (COM), U8.9 (COM), U10.9 (COM)
/CLOCK_IN: J19.1, U1.11 (SRCLK), U3.2 (1A), U4.2 (CLK), U5.11 (SRCLK), U7.11 (SRCLK), U9.11 (SRCLK)
/CLOCK_OUT: J20.1, U3.3 (1Y)
/LATCH_IN: J19.7, U1.12 (RCLK), U3.5 (2A), U4.1 (~LD), U5.12 (RCLK), U7.12 (RCLK), U9.12 (RCLK)
/LATCH_OUT: J20.7, U3.6 (2Y)
/LED_A: R2.2, U5.4 (QE)
/LED_B: R3.2, U5.5 (QF)
/LED_C: R4.2, U5.6 (QG)
/LED_D: R5.2, U9.15 (QA)
/LED_E: R1.2, U9.1 (QB)
/LED_F: R10.2, U9.2 (QC)
/LOOPBACK_A: U4.5 (G), U5.7 (QH)
/LOOPBACK_B: U4.6 (H), U9.3 (QD)
/MOTOR_A_PHASE_A: U1.15 (QA), U2.6 (I6)
/MOTOR_A_PHASE_B: U1.1 (QB), U2.5 (I5)
/MOTOR_A_PHASE_C: U1.2 (QC), U2.4 (I4)
/MOTOR_A_PHASE_D: U1.3 (QD), U2.3 (I3)
/MOTOR_B_PHASE_A: U1.4 (QE), U2.2 (I2)
/MOTOR_B_PHASE_B: U1.5 (QF), U2.1 (I1)
/MOTOR_B_PHASE_C: U1.6 (QG), U6.6 (I6)
/MOTOR_B_PHASE_D: U1.7 (QH), U6.5 (I5)
/MOTOR_C_PHASE_A: U5.15 (QA), U6.4 (I4)
/MOTOR_C_PHASE_B: U5.1 (QB), U6.3 (I3)
/MOTOR_C_PHASE_C: U5.2 (QC), U6.2 (I2)
/MOTOR_C_PHASE_D: U5.3 (QD), U6.1 (I1)
/MOTOR_D_PHASE_A: U8.6 (I6), U9.4 (QE)
/MOTOR_D_PHASE_B: U8.5 (I5), U9.5 (QF)
/MOTOR_D_PHASE_C: U8.4 (I4), U9.6 (QG)
/MOTOR_D_PHASE_D: U8.3 (I3), U9.7 (QH)
/MOTOR_E_PHASE_A: U7.15 (QA), U8.2 (I2)
/MOTOR_E_PHASE_B: U7.1 (QB), U8.1 (I1)
/MOTOR_E_PHASE_C: U7.2 (QC), U10.6 (I6)
/MOTOR_E_PHASE_D: U7.3 (QD), U10.5 (I5)
/MOTOR_F_PHASE_A: U7.4 (QE), U10.4 (I4)
/MOTOR_F_PHASE_B: U7.5 (QF), U10.3 (I3)
/MOTOR_F_PHASE_C: U7.6 (QG), U10.2 (I2)
/MOTOR_F_PHASE_D: U7.7 (QH), U10.1 (I1)
/MOTOR_IN: J19.3, U1.14 (SER)
/MOTOR_OUT: J20.3, U3.11 (4Y)
/MOTOR_OUT_PRE_BUFFER: U3.12 (4A), U7.9 (QH')
/OUT_A_PHASE_A: J3.1, U2.11 (O6)
/OUT_A_PHASE_B: J3.2, U2.12 (O5)
/OUT_A_PHASE_C: J3.3, U2.13 (O4)
/OUT_A_PHASE_D: J3.4, U2.14 (O3)
/OUT_B_PHASE_A: J5.1, U2.15 (O2)
/OUT_B_PHASE_B: J5.2, U2.16 (O1)
/OUT_B_PHASE_C: J5.3, U6.11 (O6)
/OUT_B_PHASE_D: J5.4, U6.12 (O5)
/OUT_C_PHASE_A: J6.1, U6.13 (O4)
/OUT_C_PHASE_B: J6.2, U6.14 (O3)
/OUT_C_PHASE_C: J6.3, U6.15 (O2)
/OUT_C_PHASE_D: J6.4, U6.16 (O1)
/OUT_D_PHASE_A: J7.1, U8.11 (O6)
/OUT_D_PHASE_B: J7.2, U8.12 (O5)
/OUT_D_PHASE_C: J7.3, U8.13 (O4)
/OUT_D_PHASE_D: J7.4, U8.14 (O3)
/OUT_E_PHASE_A: J12.1, U8.15 (O2)
/OUT_E_PHASE_B: J12.2, U8.16 (O1)
/OUT_E_PHASE_C: J12.3, U10.11 (O6)
/OUT_E_PHASE_D: J12.4, U10.12 (O5)
/OUT_F_PHASE_A: J13.1, U10.13 (O4)
/OUT_F_PHASE_B: J13.2, U10.14 (O3)
/OUT_F_PHASE_C: J13.3, U10.15 (O2)
/OUT_F_PHASE_D: J13.4, U10.16 (O1)
/SENSOR_A: J8.3, R6.2, U4.11 (A)
/SENSOR_B: J9.3, R7.2, U4.12 (B)
/SENSOR_C: J10.3, R8.2, U4.13 (C)
/SENSOR_D: J11.3, R9.2, U4.14 (D)
/SENSOR_E: J14.3, R11.2, U4.3 (E)
/SENSOR_F: J15.3, R12.2, U4.4 (F)
/SENSOR_IN: J20.5, R14.1, U4.10 (SER)
/SENSOR_OUT: J19.5, U4.9 (QH)
GND: C1.1, C2.2, C3.2, C4.2, C5.2, C6.2, C7.2, C8.2, C9.1, C10.1, C11.2, C12.1, D1.1 (K), D2.1 (K), D3.1 (K), D4.1 (K), D5.1 (K), D6.1 (K), J8.1, J9.1, J10.1, J11.1, J14.1, J15.1, J17.1, J17.2, J19.2, J19.4, J19.6, J19.8, J20.2, J20.4, J20.6, J20.8, R14.2, U1.8 (GND), U1.13 (~OE), U2.7 (I7), U2.8 (GND), U3.1 (1nOE), U3.4 (2nOE), U3.7 (GND), U3.9 (3A), U3.10 (3nOE), U3.13 (4nOE), U4.8 (GND), U4.15 (CLKIN), U5.8 (GND), U5.13 (~OE), U6.7 (I7), U6.8 (GND), U7.8 (GND), U7.13 (~OE), U8.7 (I7), U8.8 (GND), U9.8 (GND), U9.13 (~OE), U10.7 (I7), U10.8 (GND)
unnamed: D1.2 (A), R2.1
unnamed: D2.2 (A), R3.1
unnamed: D3.2 (A), R4.1
unnamed: D4.2 (A), R5.1
unnamed: D5.2 (A), R1.1
unnamed: D6.2 (A), R10.1
unnamed: U1.9 (QH'), U5.14 (SER)
unnamed: U5.9 (QH'), U9.14 (SER)
unnamed: U7.14 (SER), U9.9 (QH')

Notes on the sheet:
JLCPCB Assembly Tooling Holes
TPL7407L or TPL7407LA will work. OUT7 is avoided because the datasheet recommends an external flyback diode for TPL7407L, and we have spare channels we can use instead.
Do not use O7 on TPL7407L (see note above)
Motor data does not need to be buffered for transmission reasons (it is 1:1 from one board to the next, not bussed), but it is buffered to keep timing in sync with the buffered clock. 74HC595 chaining relies on narrow propagation delay > hold time margin to work, so we need to be cognizant of anyth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


Board: 2 copper layers, 198.1 x 30.5 mm, 65 parts (0 on the bottom side), 83 nets.

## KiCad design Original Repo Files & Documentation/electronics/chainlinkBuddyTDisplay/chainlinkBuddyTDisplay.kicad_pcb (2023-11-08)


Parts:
C1: 10uF; C_1206_3216Metric_Pad1.33x1.80mm_HandSolder
C2: 22uF; C_1206_3216Metric_Pad1.33x1.80mm_HandSolder
H1, H2, H3, H4: MountingHole_Pad; MountingHole_3.2mm_M3_ISO7380_Pad
J1: Output; IDC-Header_2x04_P2.54mm_Vertical
J2: Screw_Terminal_01x03; Generic-5.08-3P
J3: Barrel_Jack_Switch; PJ-202A
J7: Conn_01x04; PinHoles_1x04_P2.54mm_NoSilk
U1: TTGO_TDisplay; T-DISPLAY_extra_pins_labeled_double
U2: LM7805_TO220; TO-220-3_Vertical
Z1: polarity label; Symbol_Barrel_Polarity

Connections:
+3V3: J2.1, U1.12 (3V3)
+5V: C2.1, U1.13 (5V), U2.3 (VO)
+12V: C1.1, J2.3, J3.1, J7.1, J7.2, J7.3, J7.4, U2.1 (VI)
/CLOCK: J1.1, U1.18 (GPIO33)
/LATCH: J1.7, U1.17 (GPIO25)
/MOTOR_DATA: J1.3, U1.19 (GPIO32)
/SENSOR_DATA: J1.5, U1.20 (GPIO39)
GND: C1.2, C2.2, H1.1, H2.1, H3.1, H4.1, J1.2, J1.4, J1.6, J1.8, J2.2, J3.2, U1.1 (GND), U1.2 (GND), U1.10 (GND), U1.11 (GND), U1.14 (GND), U2.2 (GND)


Board: 2 copper layers, 74.9 x 49.5 mm, 13 parts (1 on the bottom side), 8 nets.

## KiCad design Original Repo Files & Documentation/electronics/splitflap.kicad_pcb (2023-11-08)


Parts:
C1, C3: 100uF; CP_Radial_D8.0mm_P3.50mm
C2: 0.1uF; C_Rect_L7.0mm_W2.5mm_P5.00mm
CON1: MOTOR_PWR; PJ-202A
D1: Mot+; LED_D3.0mm
D2: 5V; LED_D3.0mm
J1: EXP. IN; Pin_Header_Straight_2x07_Pitch2.54mm_IDC_Shrouded
J2: EXP. OUT; Pin_Header_Straight_2x07_Pitch2.54mm_IDC_Shrouded
JP1: VIN <-> 12V; Pin_Header_Straight_1x02_Pitch2.54mm
JP2: LED_Jumper; SolderJumper-2_P1.3mm_Bridged_Pad1.0x1.5mm
P1, P2, P3, P4: CONN_01X05; JST_XH_2-5mm_5pin
P6, P7, P8, P10: CONN_01X04; Pin_Header_Straight_1x04
R1: 2.2k; R_Axial_DIN0204_L3.6mm_D1.6mm_P7.62mm_Horizontal
R3, R4, R5, R6, R10: 47k; R_Axial_DIN0204_L3.6mm_D1.6mm_P7.62mm_Horizontal
R7: 220; R_Axial_DIN0204_L3.6mm_D1.6mm_P7.62mm_Horizontal
R9: 470; R_Axial_DIN0204_L3.6mm_D1.6mm_P7.62mm_Horizontal
U1: arduino_uno_shield
U2, U4: MIC5842; DIP-18_W7.62mm
U3: 74HC165; 74HC165_DIP-16_W7.62mm
U5, U6, U7, U8: WS2812B; LED_WS2812B_PLCC4_5.0x5.0mm_P3.2mm
Z1, Z2, Z3: MOUNT; M4_mount
Z4: ribbon cable (BOM only); Dummy_Empty
Z101: polarity marker; PolarityCenterPositive

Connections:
+5V: C2.1, C3.1, J1.5, J1.6, J2.5, J2.6, P7.1, P7.2, P7.3, P7.4, R3.1, R4.1, R5.1, R6.1, R7.2, U1.ISP2 (ICSP_VCC), U2.5 (VDD), U3.16 (VCC), U4.5 (VDD), U5.1 (VDD), U6.1 (VDD), U7.1 (VDD), U8.1 (VDD)
+12V: C1.1, CON1.1, J1.1, J1.2, J2.1, J2.2, JP1.1, P1.5, P2.5, P3.5, P4.5, R1.2, U2.10 (K), U4.10 (K)
/DBGLED_IN: J1.12, R9.2, U5.4 (DIN)
/DBGLED_OUT: J2.12, U8.2 (DOUT)
/MOTOR_DATA_IN: J1.7, U1.ISP4 (ICSP_MOSI), U2.3 (SIN)
/MOTOR_DATA_OUT: J2.7, U4.6 (SOUT)
/MOTOR_LATCH: J1.8, J2.8, U1.D4, U2.7 (STR), U4.7 (STR)
/SENSE1: P6.1, R6.2, U3.11 (A)
/SENSE2: P6.2, R5.2, U3.12 (B)
/SENSE3: P6.3, R4.2, U3.13 (C)
/SENSE4: P6.4, R3.2, U3.14 (D)
/SENSOR_DATA_IN: J2.9, R10.1, U3.10 (SER)
/SENSOR_DATA_OUT: J1.9, U1.ISP1 (ICSP_MISO), U3.9 (QH)
/SENSOR_LATCH: J1.10, J2.10, U1.D5, U3.1 (~LD)
/SPI_CLOCK: J1.11, J2.11, U1.ISP3 (ICSP_SCK), U2.2 (CLK), U3.2 (CLK), U4.2 (CLK)
unnamed: D1.1 (K), D2.1 (K), JP2.2
unnamed: D1.2 (A), R1.1
unnamed: D2.2 (A), R7.1
unnamed: P1.1, U2.18 (OUT1)
unnamed: P1.2, U2.17 (OUT2)
unnamed: P1.3, U2.16 (OUT3)
unnamed: P1.4, U2.15 (OUT4)
unnamed: P2.1, U2.14 (OUT5)
unnamed: P2.2, U2.13 (OUT6)
unnamed: P2.3, U2.12 (OUT7)
unnamed: P2.4, U2.11 (OUT8)
unnamed: P3.1, U4.18 (OUT1)
unnamed: P3.2, U4.17 (OUT2)
unnamed: P3.3, U4.16 (OUT3)
unnamed: P3.4, U4.15 (OUT4)
unnamed: P4.1, U4.14 (OUT5)
unnamed: P4.2, U4.13 (OUT6)
unnamed: P4.3, U4.12 (OUT7)
unnamed: P4.4, U4.11 (OUT8)
unnamed: P10.1, U3.3 (E)
unnamed: P10.2, U3.4 (F)
unnamed: P10.3, U3.5 (G)
unnamed: P10.4, U3.6 (H)
unnamed: R9.1, U1.D6
unnamed: U2.6 (SOUT), U4.3 (SIN)
unnamed: U5.2 (DOUT), U6.4 (DIN)
unnamed: U6.2 (DOUT), U7.4 (DIN)
unnamed: U7.2 (DOUT), U8.4 (DIN)

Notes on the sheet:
EXPANSION PORT

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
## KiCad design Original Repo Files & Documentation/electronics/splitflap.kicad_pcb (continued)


Board: 2 copper layers, 96.0 x 48.0 mm, 39 parts (1 on the bottom side), 45 nets.

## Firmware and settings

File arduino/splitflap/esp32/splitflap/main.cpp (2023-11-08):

/*
   Copyright 2020 Scott Bezek and the splitflap contributors

   Licensed under the Apache License, Version 2.0 (the "License");
   you may not use this file except in compliance with the License.
   You may obtain a copy of the License at

       http://www.apache.org/licenses/LICENSE-2.0

   Unless required by applicable law or agreed to in writing, software
   distributed under the License is distributed on an "AS IS" BASIS,
   WITHOUT WARRANTIES OR CONDITIONS OF ANY KIND, either express or implied.
   See the License for the specific language governing permissions and
   limitations under the License.
*/

#include <Arduino.h>
#include <TFT_eSPI.h>
#include <Wire.h>
#include <WiFi.h>
#include <ESP32Time.h>

#include "config.h"

#include "../core/splitflap_task.h"
#include "display_task.h"
#include "serial_task.h"
#include <Ticker.h>

// Create Tickers
Ticker displayTicker; 
Ticker ntpTicker;
Ticker buttonTicker;

// Setup Tasks
SplitflapTask splitflapTask(1, LedMode::AUTO);
SerialTask serialTask(splitflapTask, 0);

// Create Real Time Clock
ESP32Time rtc;
// Booleans for handling button presses
volatile long nextAllowedButtonPress;
volatile bool buttonPressAllowed = false;

#include "webserver_task.h"
WebServerTask webserverTask(splitflapTask, serialTask, 1);

#if ENABLE_DISPLAY
DisplayTask displayTask(splitflapTask, 0);
#endif

#ifdef CHAINLINK_BASE
#include "../base/base_supervisor_task.h"
BaseSupervisorTask baseSupervisorTask(splitflapTask, serialTask, 0);
#endif

#if MQTT
#include "mqtt_task.h"
MQTTTask mqttTask(splitflapTask, serialTask, 0);
#endif

#if HTTP
#include "http_task.h"
HTTPTask httpTask(splitflapTask, displayTask, serialTask, 0);
#endif

// Function that resets the buttonPressAllowed boolean
void buttonStateMachine() {
  if (millis() > nextAllowedButtonPress) {
    buttonPressAllowed = true;
  }
}

// Function that connects to WiFi
void connectToWiFi() {
  // Connect to Wi-Fi
  WiFi.begin(WIFI_SSID, WIFI_PASSWORD);
  
  // Wait for connection with a timeout
  unsigned long startMillis = millis();
  while (WiFi.status() != WL_CONNECTED) {
    delay(1000);
    serialTask.log("Connecting to WiFi...");
    
    // Check for a timeout (e.g., 30 seconds)
    if (millis() - startMillis > 30000) {
      serialTask.log("Wi-Fi connection timed out");
      // Handle the timeout (e.g., display a message or take another action)
      displayTask.wifi_failed = true;
      break;
    }
  }

  // Check the final connection status
  if (WiFi.status() == WL_CONNECTED) {
    serialTask.log("Connected to Wi-Fi");
    // Print the device IP address to the serial log
    serialTask.log(WiFi.localIP().toString().c_str());
  } else {
    serialTask.log("Wi-Fi connection failed");
    // Handle the connection failure (e.g., retry, display an error message, etc.)
  }
}

// Function that shows the current time on the splitflap display
// and handles button presses, lunch time, home time and tinker time
void showCurrentTime() {
  // Get the current time
  int curr_time = rtc.getTime("%H%M").toInt();

  if (!webserverTask.displayingMessage) {
        // Handle time display logic here
        // We must send the string in lower case, as capital letters are not supported.
        if (buttonPressAllowed) {
          // Button Pressed
          splitflapTask.showString("ooh...", NUM_MODULES, false);
          serialTask.log("BUTTON PRESSED");
          delay(5000); // Allow time (5 seconds) for message to be rotated and read
          splitflapTask.showString("..baby", NUM_MODULES, false);
          delay(5000); // Allow time (5 seconds) for message to be rotated and read
          nextAllowedButtonPress = millis() + 1800000; // Set the next allowed button press time to 30 minutes from now
          buttonPressAllowed = false;
        } else if (curr_time > 1158 && curr_time < 1202) {
          //Lunch Time
          splitflapTask.showString("lunch.", NUM_MODULES, false);
          serialTask.log("LUNCH.");
        } else if (curr_time > 1658 && curr_time < 1702) {
          // Home Time
          splitflapTask.showString(" home ", NUM_MODULES, false);
          serialTask.log(" HOME ");
        } else if (rtc.getDayofWeek() == TINKER_DAY && (curr_time > 1758 && curr_time < 1810)) {
          // Tinker Time
          splitflapTask.showString("tinker", NUM_MODULES, false);
          serialTask.log("TINKER");
        } else {
          // Show the current time
          splitflapTask.showString(rtc.getTime(" %H%M ").c_str(), NUM_MODULES, false);
          serialTask.log(rtc.getTime(" %H%M ").c_str());
        }
    } else {
        // Check if it's time to stop displaying the web message
        unsigned long currentTime = millis();
        if (currentTime - webserverTask.messageDisplayStartTime >= webserverTask.messageDisplayDuration) {
            webserverTask.displayingMessage = false;
        }
    }
}

// Function that sets the timezone to GMT/BST
void setTimezone(String timezone){
  serialTask.log("Setting Timezone to GMT/BST");
  setenv("TZ",timezone.c_str(),1);  //  Now adjust the TZ.  Clock settings are adjusted to show the new local time
  tzset();
}

// Function that sets up the NTP system
void setupCalibrateNTP() {
  configTime(0, 0, "ntp.kent.ac.uk", "pool.ntp.org");
  struct tm timeinfo;
  if (getLocalTime(&timeinfo)){
    rtc.setTimeStruct(timeinfo);
    displayTask.displayClockStatus("NTP Clock Connected", TFT_GREEN);
  } else {
    displayTask.displayClockStatus("NTP Clock Failed", TFT_RED);
  }
  // Set the timezone for Europe/London to adjust for daylight savings
  // Timezone strings can be found here: https://github.com/nayarsystems/posix_tz_db/blob/master/zones.csv
  setTimezone("GMT0BST,M3.5.0/1,M10.5.0");
}

// Function that sets up the Ticker to call setupCalibrateNTP once at 3am
void ntpTickerFunction() {
  ntpTicker.attach(86400, setupCalibrateNTP);
  setupCalibrateNTP();
}

// Main setup function
void setup() {
  serialTask.begin();
  splitflapTask.begin();

  #if ENABLE_DISPLAY
  displayTask.begin();
  #endif

  #if MQTT
  mqttTask.begin();
  #endif

  #if HTTP
  httpTask.begin();
  #endif

  #ifdef CHAINLINK_BASE
  baseSupervisorTask.begin();
  #endif

  // Start WiFi connection
  connectToWiFi();

  // Start the NTP System
  setupCalibrateNTP();
  // Get the current time
  int curr_time = rtc.getTime("%H%M").toInt();
  // Calculate the number of seconds until 3am
  int secUntil3am = 2400 - curr_time + 180;
  // Set up the Ticker to call ntpTickerFunction once at 3am
  // This ensures that the clock is calibrated every day at 3am
  ntpTicker.once(secUntil3am, ntpTickerFunction);

  // Set up the Ticker to call showCurrentTime every 1 second
  displayTicker.attach(1, showCurrentTime);

  // Setup the button
  pinMode(BUTTON_PIN, INPUT_PULLUP);
  // Make sure button press is only allowed every 30 minutes
  // buttonTicker.attach(1800, buttonTimer);
  nextAllowedButtonPress = millis() + 5000;
  attachInterrupt(BUTTON_PIN, buttonStateMachine, FALLING);

  webserverTask.begin();
  // Delete the default Arduino loopTask to free up Core 1
  vTaskDelete(NULL);
}

void loop() {
  assert(false);
}

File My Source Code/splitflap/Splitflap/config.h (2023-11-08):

#pragma once

#include <Arduino.h>

/***** CONFIGURATION *****/

// 1) Mode
#define SENSOR_TEST false

// 2) General Settings
#ifndef NUM_MODULES
#define NUM_MODULES (12)
#endif

// Whether to force a full rotation when the same letter is specified again
#define FORCE_FULL_ROTATION true

// Whether to use/expect a home sensor. Enable for auto-calibration via home
// sensor feedback. Disable for basic open-loop control (useful when first
// testing the split-flap, since home calibration can be tricky to fine tune)
#define HOME_CALIBRATION_ENABLED true

// 3) Flap Contents & Order
#define NUM_FLAPS (40)

// This should match the order of flaps on the spool, with the first being the
// "home" flap.
const uint8_t flaps[NUM_FLAPS] = {
  ' ',
  'a', 'b', 'c', 'd', 'e', 'f', 'g', 'h', 'i', 'j', 'k', 'l', 'm',
  'n', 'o', 'p', 'q', 'r', 's', 't', 'u', 'v', 'w', 'x', 'y', 'z',
  '0', '1', '2', '3', '4', '5', '6', '7', '8', '9',
  '.',
  ',',
  '\'',
};

// 4) Hardware configuration and features
#ifndef SPLITFLAP_PIO_HARDWARE_CONFIG
  // Note: these values are only used in the Arduino IDE. For PlatformIO,
  // hardware configuration is set by the environment, in platformio.ini.
  #define SPI_IO true
  #define REVERSE_MOTOR_DIRECTION false
  #define NEOPIXEL_DEBUGGING_ENABLED true
  #define SSD1306_DISPLAY false
  #define INA219_POWER_SENSE false
#endif

// 5) Board-dependent Default Settings

#if defined(__AVR_ATmega168__) || defined(__AVR_ATmega328P__)
  #if SPI_IO
  #define NEOPIXEL_PIN 6
  #else
  #define NEOPIXEL_PIN 3
  #endif
  #define MONITOR_SPEED 38400
#elif defined(__AVR_ATmega2560__)
  #define NEOPIXEL_PIN 5
  #define MONITOR_SPEED 38400
#elif defined(ARDUINO_ESP8266_WEMOS_D1MINI)
  #define NEOPIXEL_PIN (D8)
  #define MONITOR_SPEED 38400
#elif defined(ESP32)
  #define NEOPIXEL_PIN (13)
  #define MONITOR_SPEED 230400
#endif

// 6) WIFI Settings
#define WIFI_SSID "microlab_IoT"
#define WIFI_PASSWORD "shibboleet"

// 7) Custom Definitions
#define TINKER_DAY  3
#define BUTTON_PIN  15


/*************************/


/**
 * Suggested Pinouts
 *
 * Arduino Uno - Basic IO - Up to 3 modules
 *    A: Motor: B0-3 = pins 8-11        Sensor: B4 = pin 12
 *    B: Motor: D4-7 = pins 4-7         Sensor: C4 = pin A4
 *    C: Motor: C0-3 = pins A0-A3       Sensor: C5 = pin A5
 *
 *    Neopixel: 3
 *
 * Arduino Uno - SPI IO (Shift Register) - Up to 12 modules
 *    4   Motor latch
 *    5   Sensor latch
 *    6   neopixel
 *    11  MOSI
 *    12  MISO
 *    13  CLK
 *
 * Arduino Mega 2560 - Basic IO - Up to 12 modules)
 *    Note the order of pins increases for some motors and decreases for others.
 *    Modules whose motor phase pins are in the opposite order are marked with a * below.
 *
 *    A: Motor: F0-3 = pins A0-A3       Sensor: G0 = pin 41
 *    B: Motor: F4-7 = pins A4-A7       Sensor: G1 = pin 40
 *    C: Motor: K0-3 = pins A8-A11      Sensor: G2 = pin 39
 *    D: Motor: K4-7 = pins A12-A15     Sensor: D7 = pin 38
 *    E: Motor: B0-3 = pins 53-50 *     Sensor: D2 = pin 19
 *    F: Motor: L0-3 = pins 49-46 *     Sensor: D3 = pin 18
 *    G: Motor: L4-7 = pins 45-42 *     Sensor: H0 = pin 17
 *    H: Motor: C0-3 = pins 37-34 *     Sensor: H1 = pin 16
 *    I: Motor: C4-7 = pins 33-30 *     Sensor: J0 = pin 15
 *    J: Motor: A4-7 = pins 29-26 *     Sensor: J1 = pin 14
 *    K: Motor: A0-3 = pins 25-22 *     Sensor: E4 = pin 2
 *    L: Motor: B4-7 = pins 10-13       Sensor: E5 = pin 3
 *
 *    Neopixel: 4
 *
 *    INA219 & SSD1306 Oled:
 *      SDA: 20
 *      SCL: 21
 *
 * ESP32 - SPI IO (Shift Register) - Up to 120+ modules:
 *     25 Latch         (out)
 *     33 CLK           (out)
 *     39 MISO          (in)
 *     32 MOSI          (out)
 *
 */


// Configuration validation and dependent settings
#if NUM_MODULES < 1
#error NUM_MODULES must be at least 1
#endif
#ifdef CHAINLINK
#define NUM_LOOPBACKS (NUM_MODULES / 3)
#define CHAINLINK_ENFORCE_LOOPBACKS 1
#endif

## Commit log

2023-11-08 Reordering Directories
    [28byj-48.scad, assert.scad, chainlinkBase.kicad_pcb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]
2023-11-08 Push remaining files
    Push all remaining files for the project.
    [10 by 8 Flaps with chars.dxf, 10 by 8 Flaps.dxf, Footprint for base.dxf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]
2023-11-08 Test B&R *RELEASE* *V* 1.0.3
    Test B&R *RELEASE* *V* 1.0.3
    [Footprint for base stand.dxf]
2023-11-08 Test B&R RELEASE V 1.0.3
    [Footprint for base.dxf]
2023-11-08 Test B&R *RELEASE* *V* 1.0.3
    [Footprint for base stand.dxf]
2023-11-08 *RELEASE* *V* 1.0.3
    [Footprint for base.dxf]
